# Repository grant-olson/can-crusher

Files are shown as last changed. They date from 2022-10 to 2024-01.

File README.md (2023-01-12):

Welcome to the repository for the most sophisticated robotic aluminum
can crusher that the world has seen!

This is the result of a hobby project that combines CAD design,
Hardware, PCB design, firmware, and software to build an over-the-top
computer-controlled can crusher. I wanted to use a wide variety of skills
on this project instead of going deep into a specific skill.

## In depth 30 minute video on the project

[The Most Technologically Advanced Aluminum Can Crusher In The World](https://youtu.be/nmYN3EZNI_g)

## The Frame

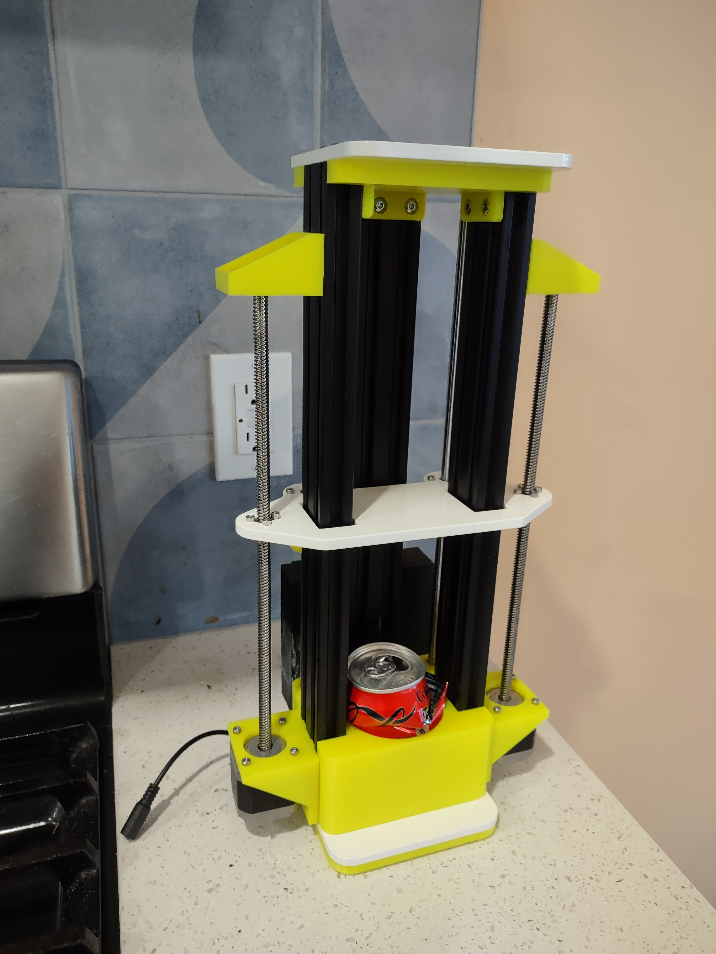
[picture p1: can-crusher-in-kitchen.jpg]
Crusher at home


The frame starts with 3 standard 2040 slotted aluminum extrusions. From there
the major structural elements, the:

* top
* bottom
* crusher plate

Are made from laser cut aluminum.

The rest of the parts are 3D printed.

All design elements are in the included FreeCAD workspace. If you just
want to cut or print the parts refer to the [stl directory](./stl) for
3D print files or the [step directory](./step) for files suitable for laser
cutting.

You will also need two stepper motors with rods and two smooth rods to
assemble the frame in its entirety.

## Stepper Control Board

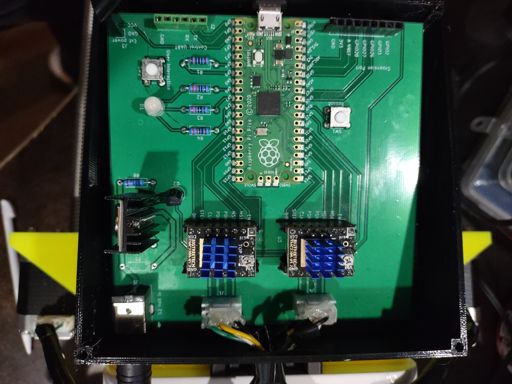
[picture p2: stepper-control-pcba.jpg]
Stepper Controller


To drive the stepper motors I've made a control board powered by a Raspberry
Pi Pico that uses TMC2209 chips to drive the steppers. This allows me to
auto-detect limits of movement.

The design is in KiCad. Gerber files are also included in the repo for
getting PCBs made.

At a high level the control board:

* Initializes the system
* Accepts a small command language over the UART interface.
* Controls the motors appropriately.

I chose the Pi Pico so that I could use the PIO subprocessors to get
extremely reliable control of the stepper signal waves. I'm able to
run those completely deterministicly based on the clock speed where
even IRQs won't affect triggering.

To build the software:

* Set up your computer to build for Pico projects.
* `cd firmware/pico`
* `mkdir build`
* `cd build`
* `cmake ..`
* `make`
* `picotool load can-crusher.uf2 && picotool reboot`

If you have stepper motors hooked up they should perform a minor
up/down jogging of the motors upon reboot. Use this to see if the
code is actually running without the admin consoles set up.

## High level control and UI

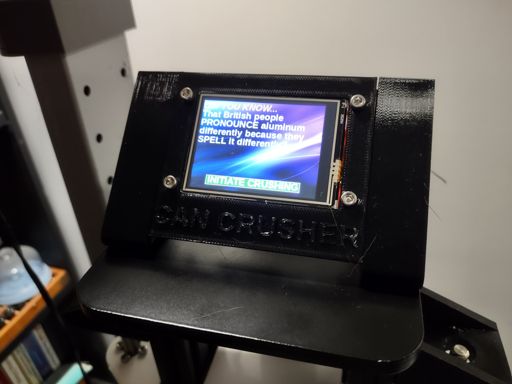
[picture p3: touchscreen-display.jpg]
Head Unit


For the high level control and UI I've written a program for a Raspberry
Pi that shows a minimal display on a TFT-LCD with touchscreen to allow users
to interact.

To make a compact display I've created a Hat for a Pi Zero board that allows
you to mount the parts together directly that is also released as a KiCad file.

Due to continuing Raspberry Pi shortages I'd like to build some
alternate versions of the control boards for other SBCs. The software
itself iswritten in python and should be portable to pretty much any
linux system. There are only 3 hardware requirements so I expect other
boards will be easy to integrate:

* Ability to have a hardware level SPI control with /dev/spidevX.X exposed.

* A kernel that supports ADS7846  touch screens and provides integration with
    `evdev` to read touch screen events.

* A hardware serial/uart port capable of running at 115200 baud.

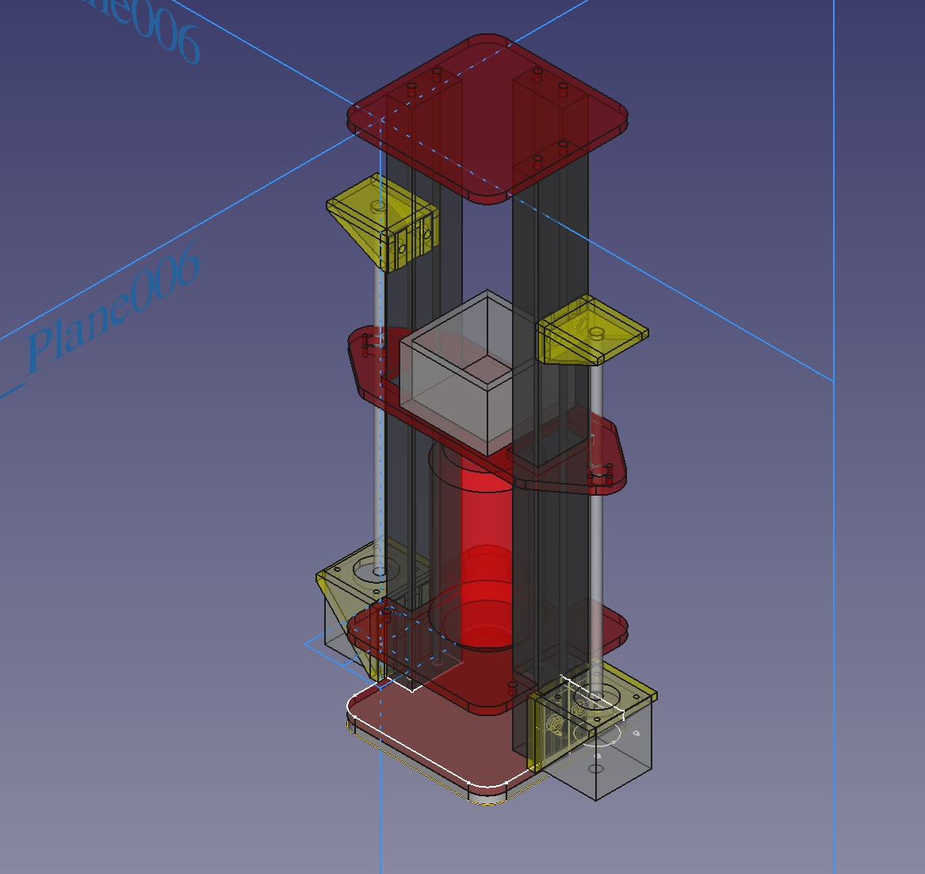
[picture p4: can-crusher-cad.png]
Cad render


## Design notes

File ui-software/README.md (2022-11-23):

#UI Software

The current UI software runs on a Raspberry Pi Zero with an attached
TFT LCD Touchscreen. There are a variety of vendors that sell the same
style 320x240 with the same pinout on Amazon, eBay, and
AliExpress. Although it can be wired up manually there is also a Pi
Hat in the kicad section of the project to make an adapter PCBA.

It communicates with the main control software via a serial connection
and receives its power from the base unit.

There are three programs that are important:

`slide-maker` pre-builds optimized versions of graphics to make it
easier to run efficiently on the moderately slow Raspberry Pi Zero.

`can-crusher-pi` runs the code for the specified head unit
configuration above.

`can-crusher-cli` provides a simple way to run the code directly from
your dev computer with a USB-to-UART dongle, which is much easier than
trying to remotely program on the Pi Zero.

The `can_crusher` directory contains the python modules that do all
the heavy work.

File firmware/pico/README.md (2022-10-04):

# Pico firmware for can crusher project.

Assuming you've set up a Pico development environment as described in
[Getting Started with
Pico](https://datasheets.raspberrypi.com/pico/getting-started-with-pico.pdf):

Then build the project standard CMake style:

```
mkdir build
cd build
cmake ..
make
```

And you will have a UF2 file ready for installation.

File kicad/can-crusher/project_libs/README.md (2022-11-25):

The following libraries are from SnapEDA and can't be included on github.

# R1966 power switch

1. Download from https://www.snapeda.com/parts/R1966ABLKBLKGR/E-Switch/view-part/

2. Extract to the subdirectory `R1966` here.

# 3522 Fuse Holder

1. Download from https://www.snapeda.com/parts/3522-2/Keystone%20Electronics/view-part/

2. Extract to the subdirectory `3522` here.

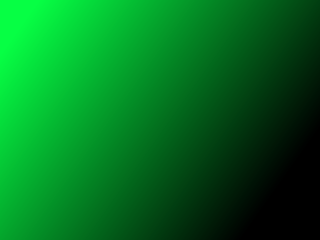
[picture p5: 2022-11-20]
ui-software/input/backgrounds/green_background.png

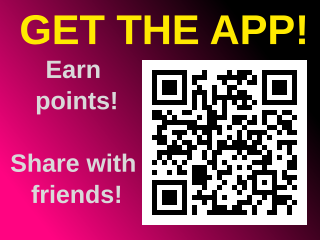
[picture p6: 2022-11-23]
ui-software/input/png/get_the_app.png

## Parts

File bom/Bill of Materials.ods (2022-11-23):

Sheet: Hardware
Part | Quantity | Function
Button Head M5 * 8mm | 22 | Attach 3D Parts to Extrusions
M5 T-Slot Nut | 22
2040 Aluminum Extrusion | 3
M5 ??? | 6 | Attach frame bottom to Extrusions
M5 ??? | 6 | Attach frame top to Extrusions
M3 ??? | 8 | Attach steppers to stepper holders
M3 ??? | 6 | Attach bearing holders to crusher plate
10mm straight rod x 350mm | 2 | Guide Rods
Nema 17 Stepper motors with 30mm threaded Rods | 2
Raspbery Pi Zero | 1 | UX computer
Bearings | 2
12 Volt power supply | 1
M3 x 14 | 4 | Connect PCB Case Front to Back

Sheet: 3D Prints
Part | Quantity
Rod Holder | 2
Frame Bottom | 1
Frame Top | 1
Frame Base | 1
Servo Holder | 2
Crusher | 1

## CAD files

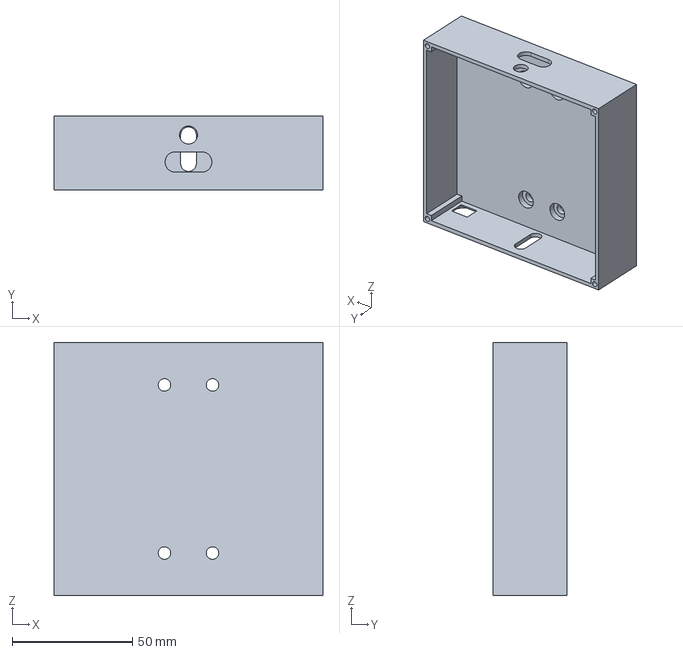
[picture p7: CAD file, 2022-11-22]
freecad/can-crusher.FCStd
112.0 x 31.0 x 105.5 mm

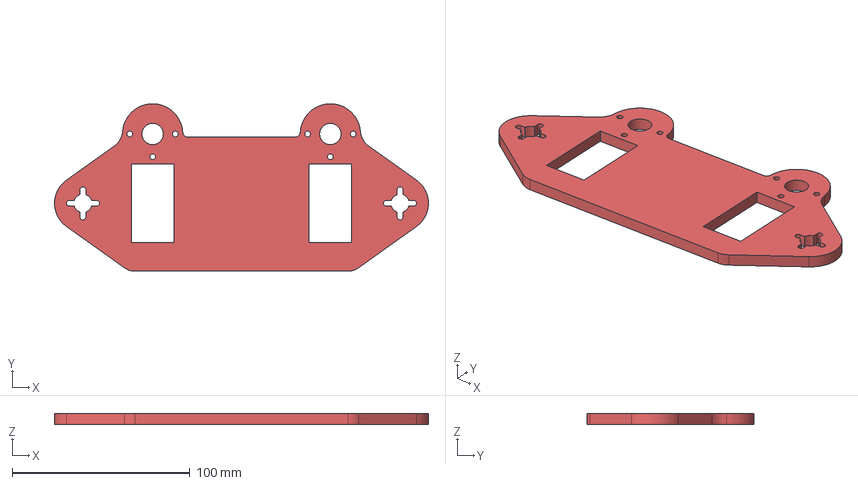
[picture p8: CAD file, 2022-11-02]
step/crusher-element-with-bearing-holders.step
210.4 x 94.2 x 6.00 mm

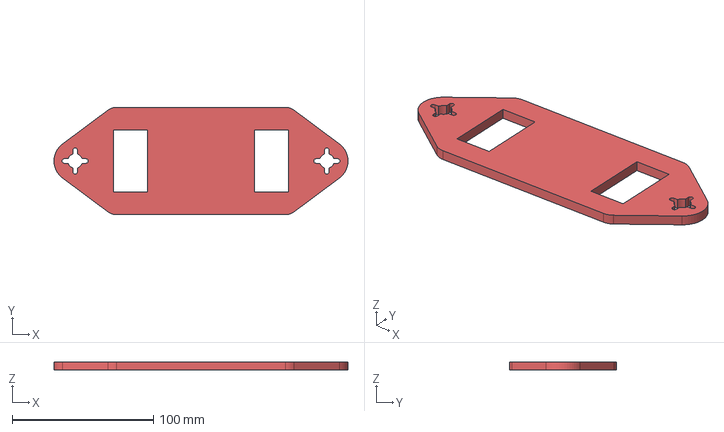
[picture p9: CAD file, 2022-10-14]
step/crusher-element-laser.step
208.3 x 76.0 x 6.00 mm

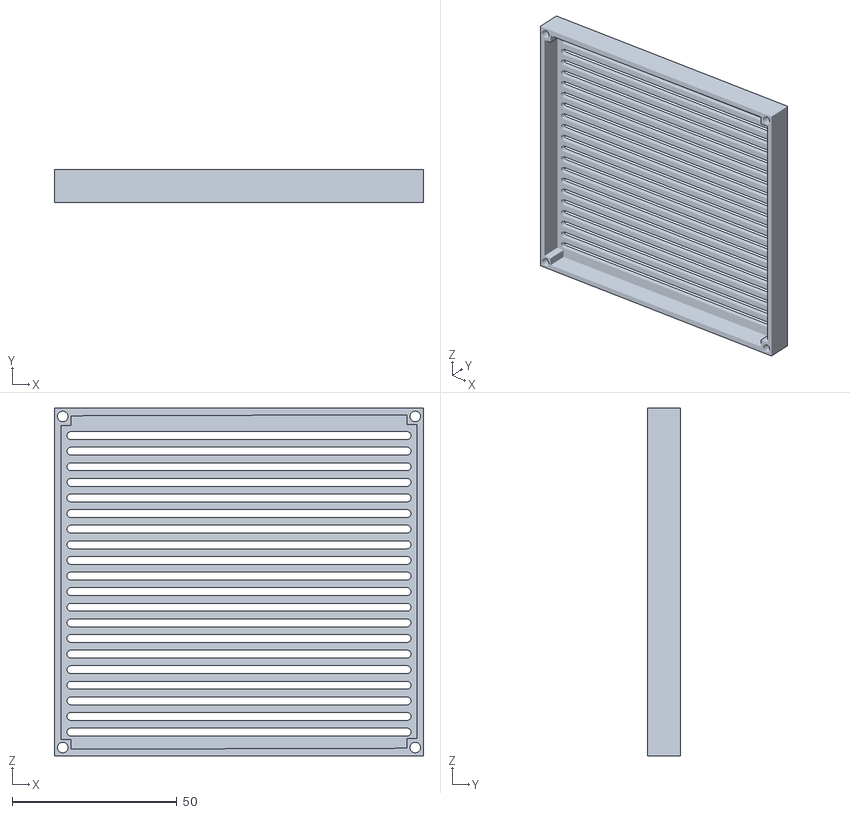
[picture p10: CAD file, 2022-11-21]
stl/pcb-holder-lid.stl
112.0 x 10.0 x 105.5

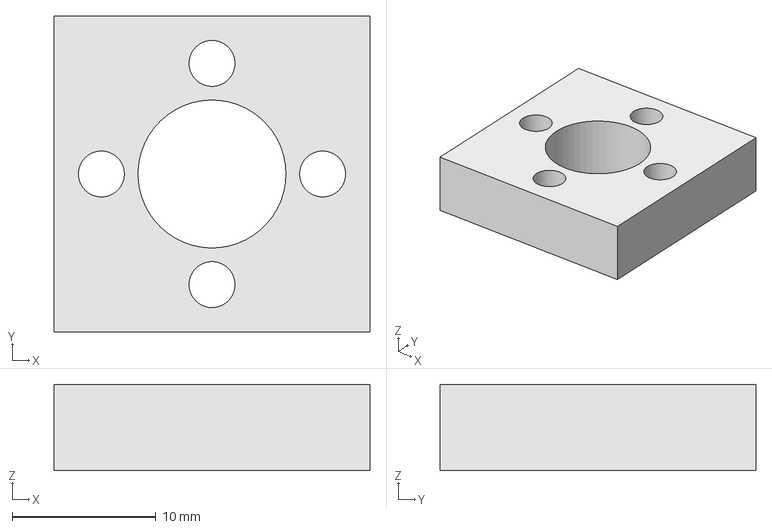
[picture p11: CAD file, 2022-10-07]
step/lead_holder_test.step
22.0 x 22.0 x 6.00 mm

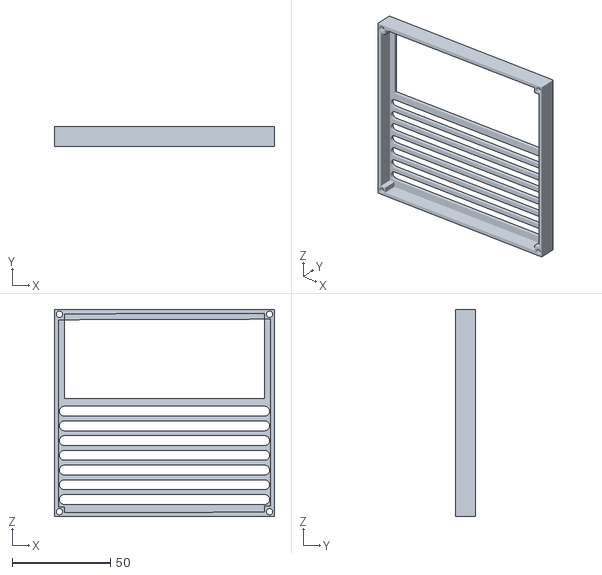
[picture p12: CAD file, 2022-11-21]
stl/ALT-pcb-holder-lid-with-dev-button-access.stl
112.0 x 10.0 x 105.5

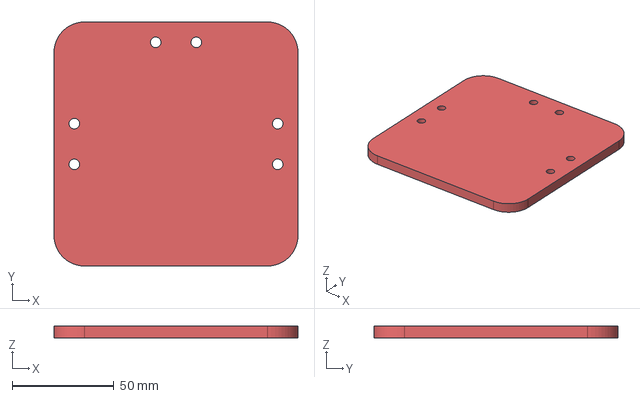
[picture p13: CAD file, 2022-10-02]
step/frame-ends.step
120.0 x 120.0 x 6.00 mm

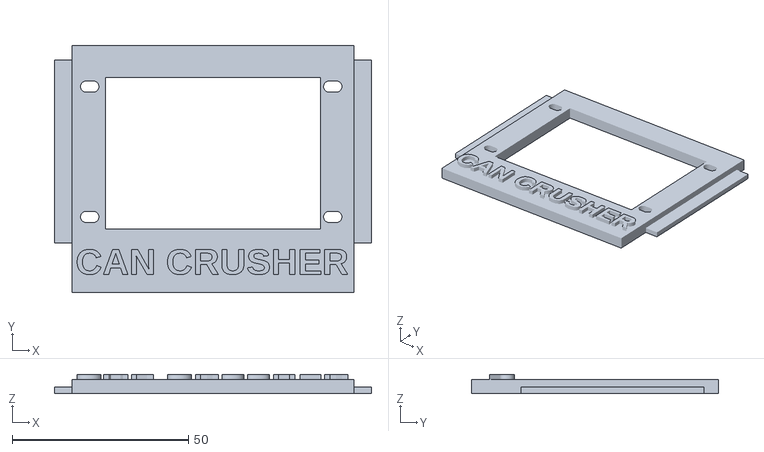
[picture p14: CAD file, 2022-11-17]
stl/touch-screen-front.stl
90.0 x 70.0 x 5.40

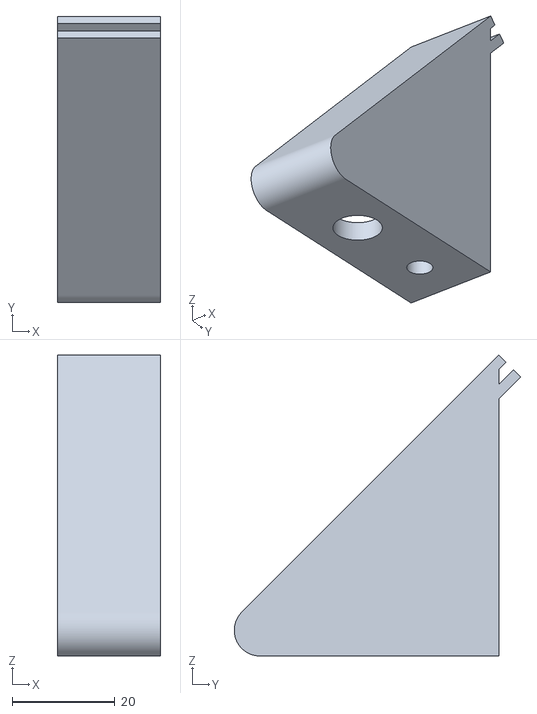
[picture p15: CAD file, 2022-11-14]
stl/touch-screen-right.stl
20.0 x 55.7 x 58.5

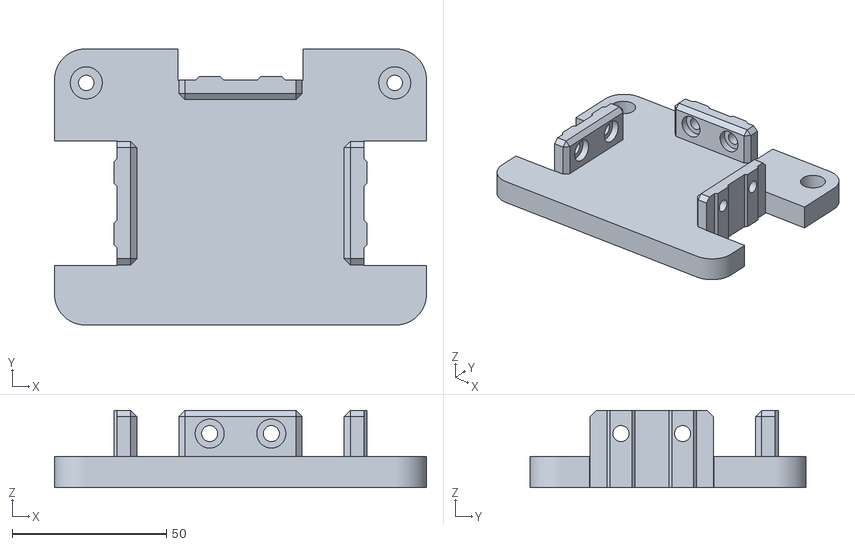
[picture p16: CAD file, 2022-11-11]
stl/smooth-rod-holder-top.stl
120.6 x 89.5 x 25.0

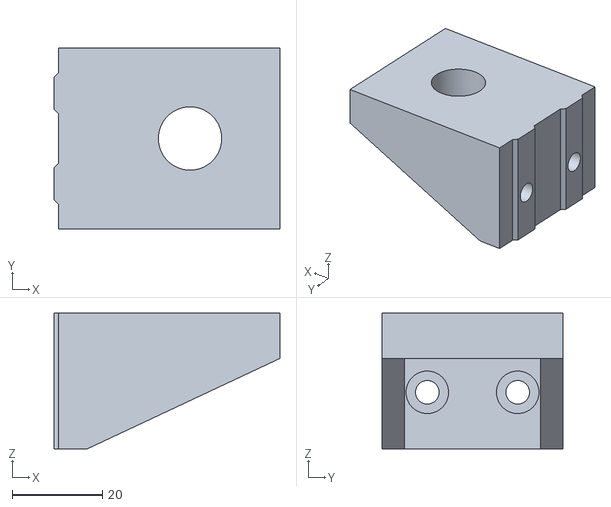
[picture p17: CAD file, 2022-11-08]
stl/rod-holder.stl
50.0 x 40.0 x 30.0

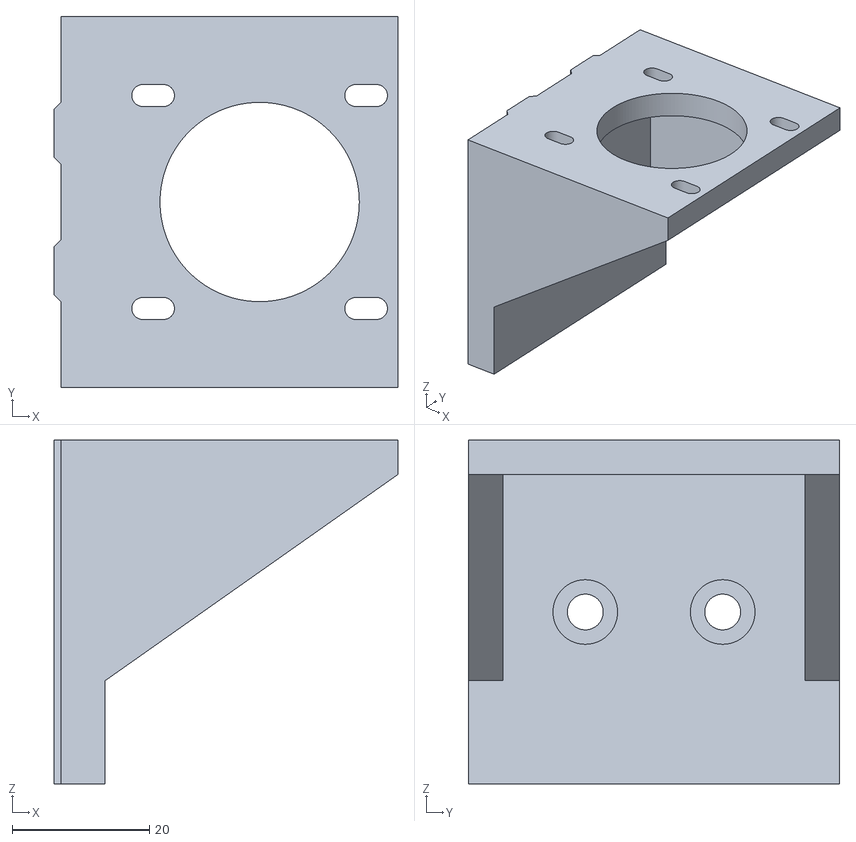
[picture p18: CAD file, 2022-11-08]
stl/stepper-holder.stl
50.0 x 54.0 x 50.0

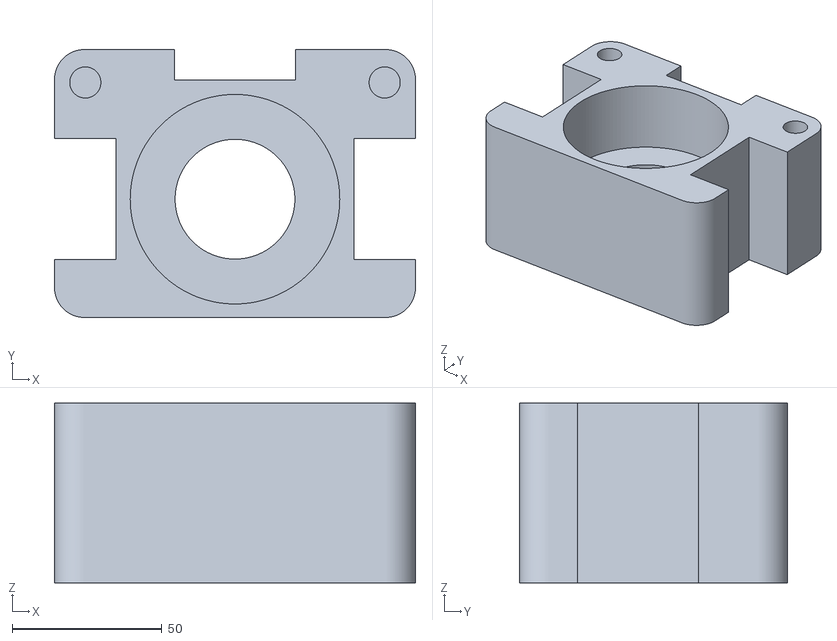
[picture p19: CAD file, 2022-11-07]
stl/can-holder.stl
120.6 x 89.5 x 60.0

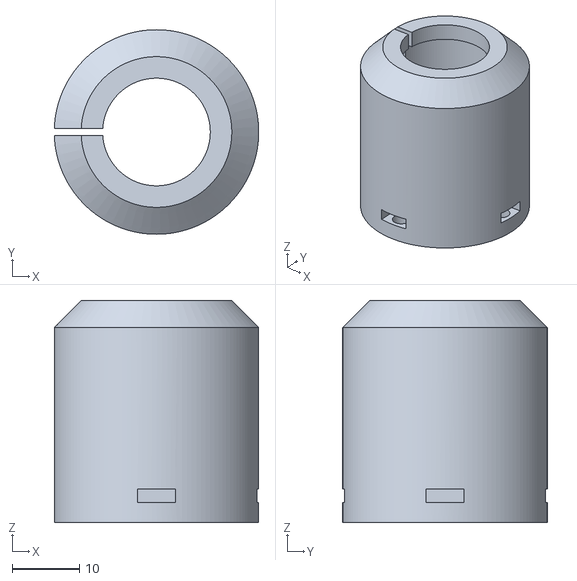
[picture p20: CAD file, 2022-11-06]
stl/vertical-bearing-holder.stl
30.4 x 30.4 x 33.0

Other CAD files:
stl/ALT-pcb-holder-pico-on-header-socket.stl
stl/pcb-holder.stl
step/crusher-element-cnc.step
stl/touch-screen-left.stl
stl/base-with-feet.stl
stl/crusher-element-with-bearing-holders.stl
stl/crusher-plate.stl
stl/frame-plates.stl
stl/test-rail-guide.stl
stl/weight-tray.stl

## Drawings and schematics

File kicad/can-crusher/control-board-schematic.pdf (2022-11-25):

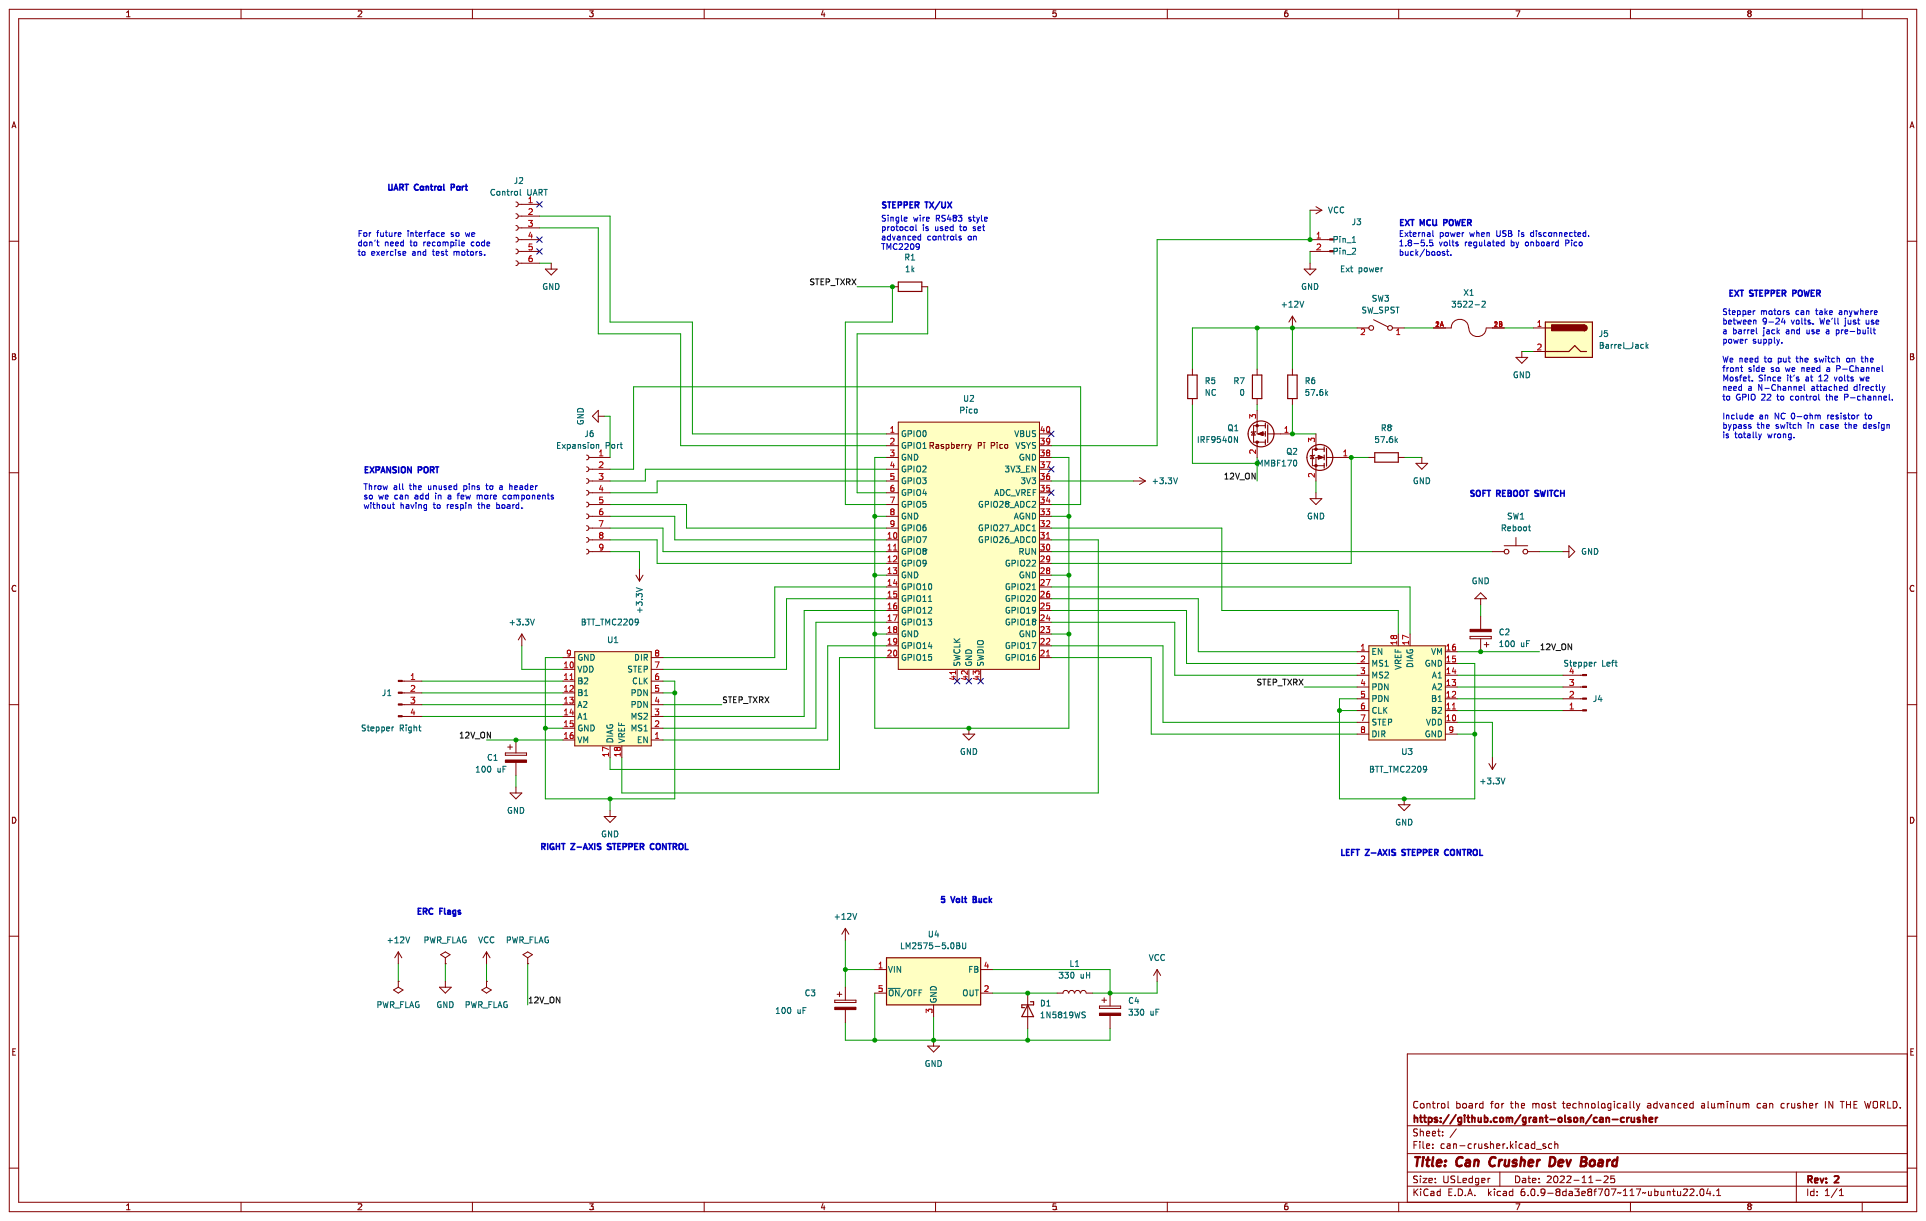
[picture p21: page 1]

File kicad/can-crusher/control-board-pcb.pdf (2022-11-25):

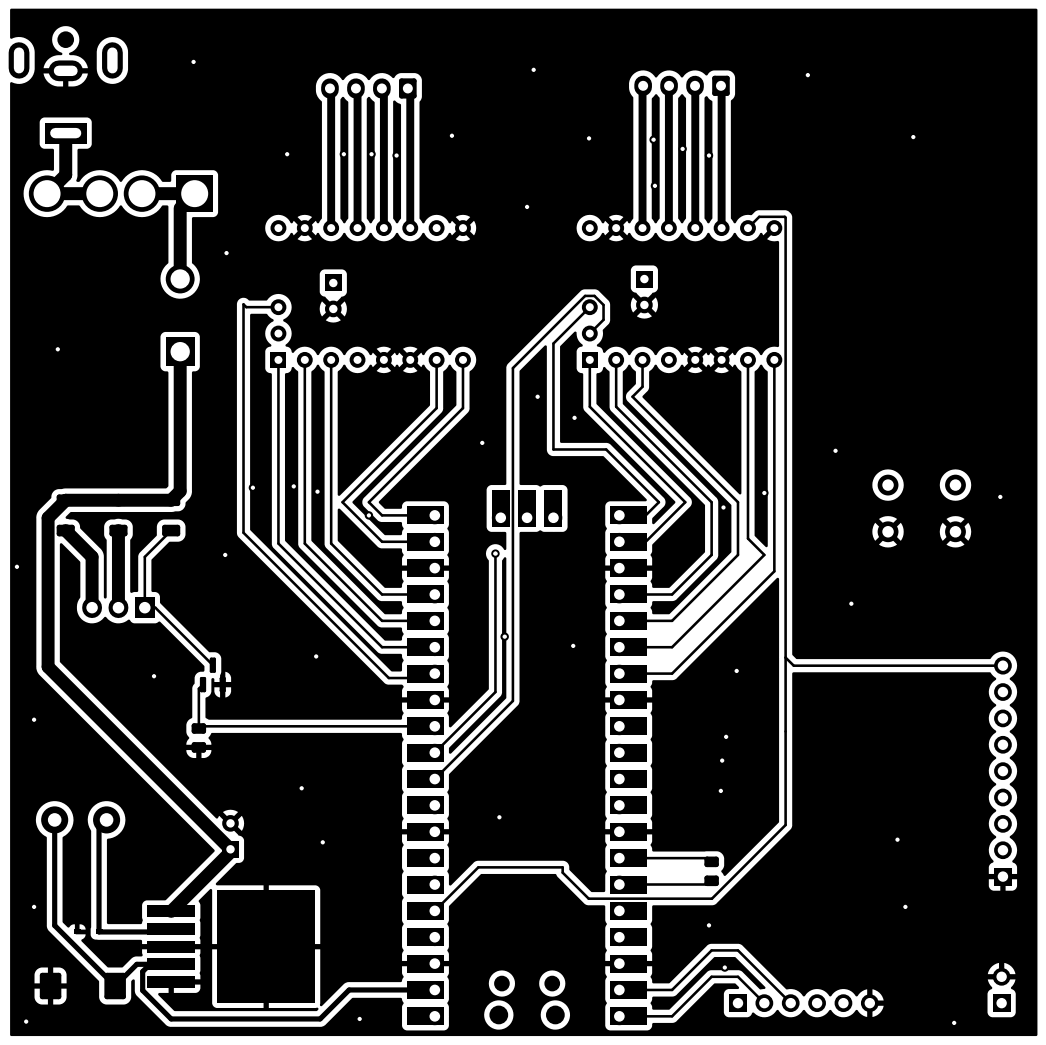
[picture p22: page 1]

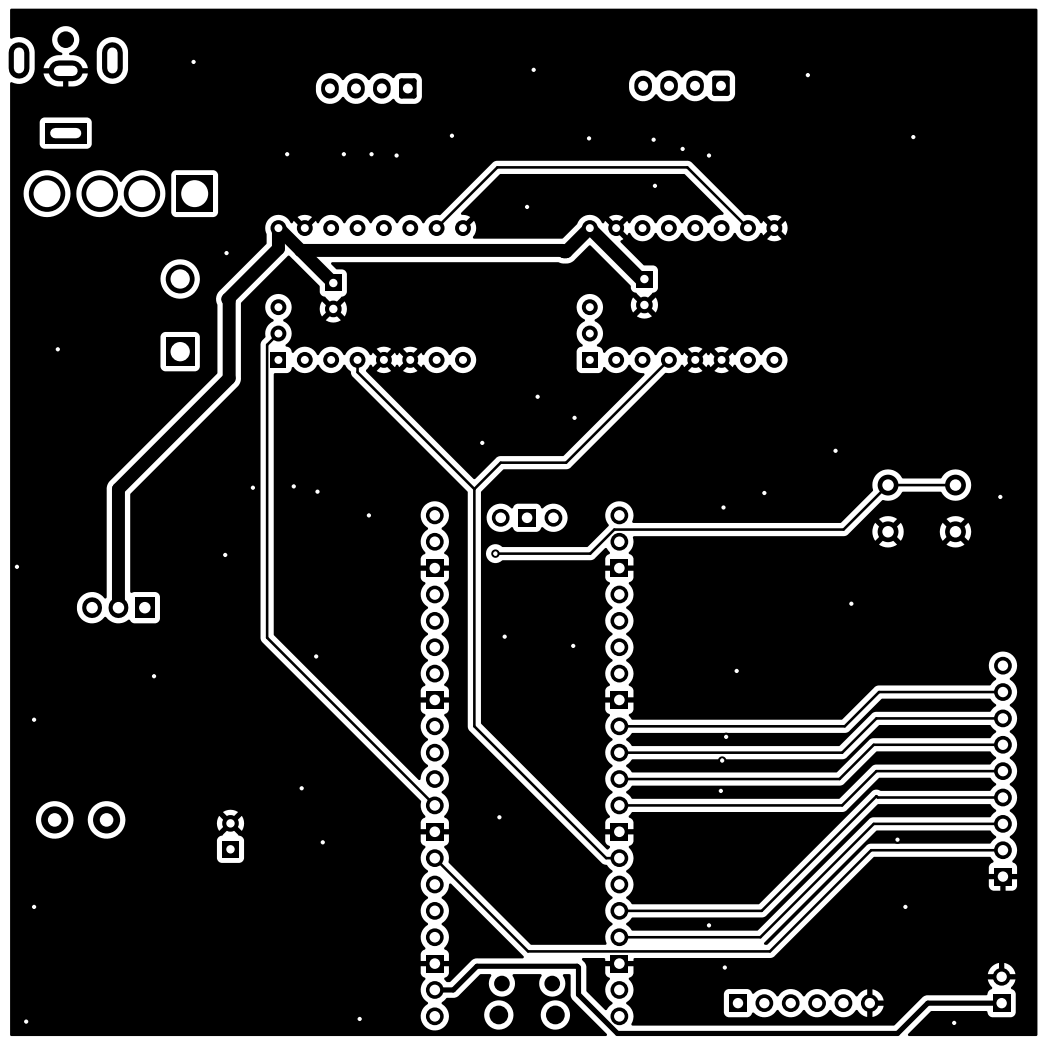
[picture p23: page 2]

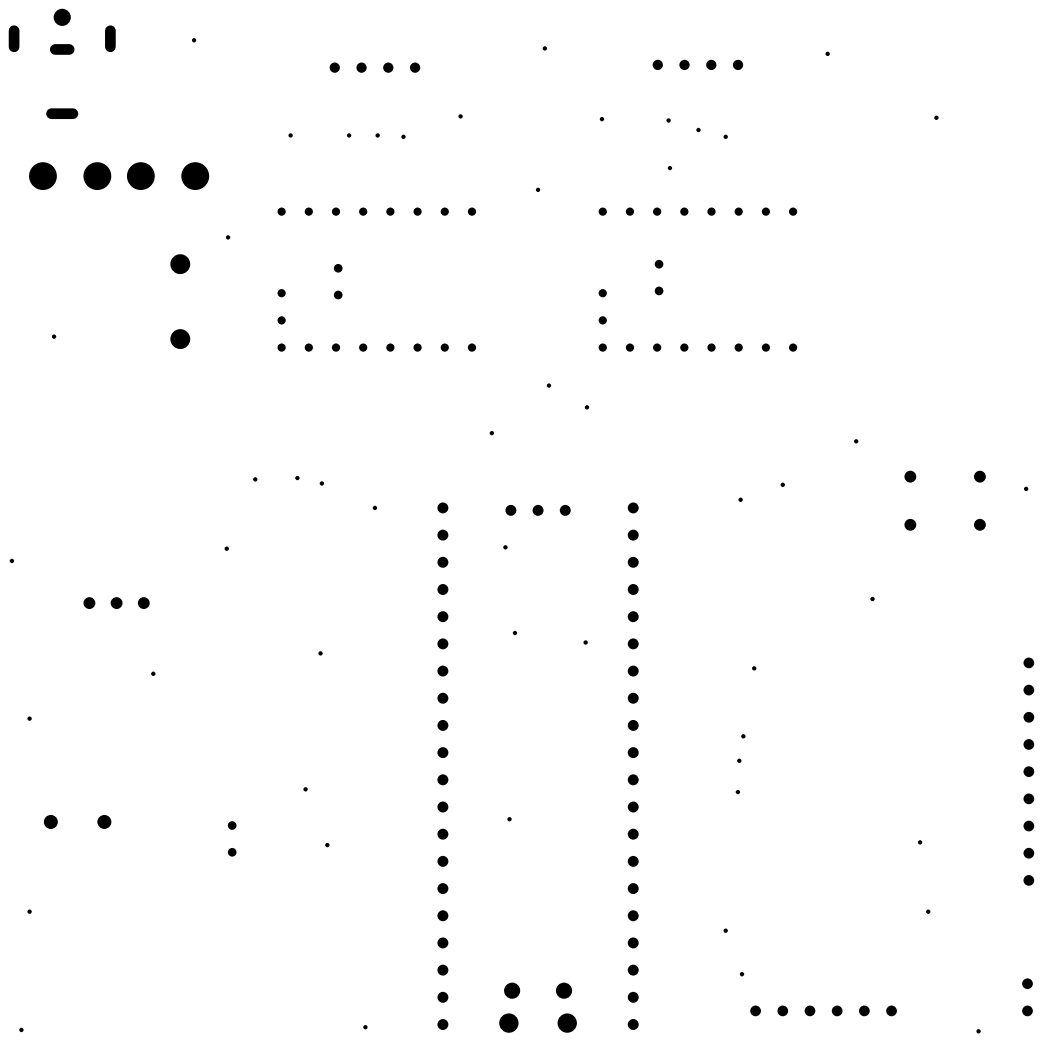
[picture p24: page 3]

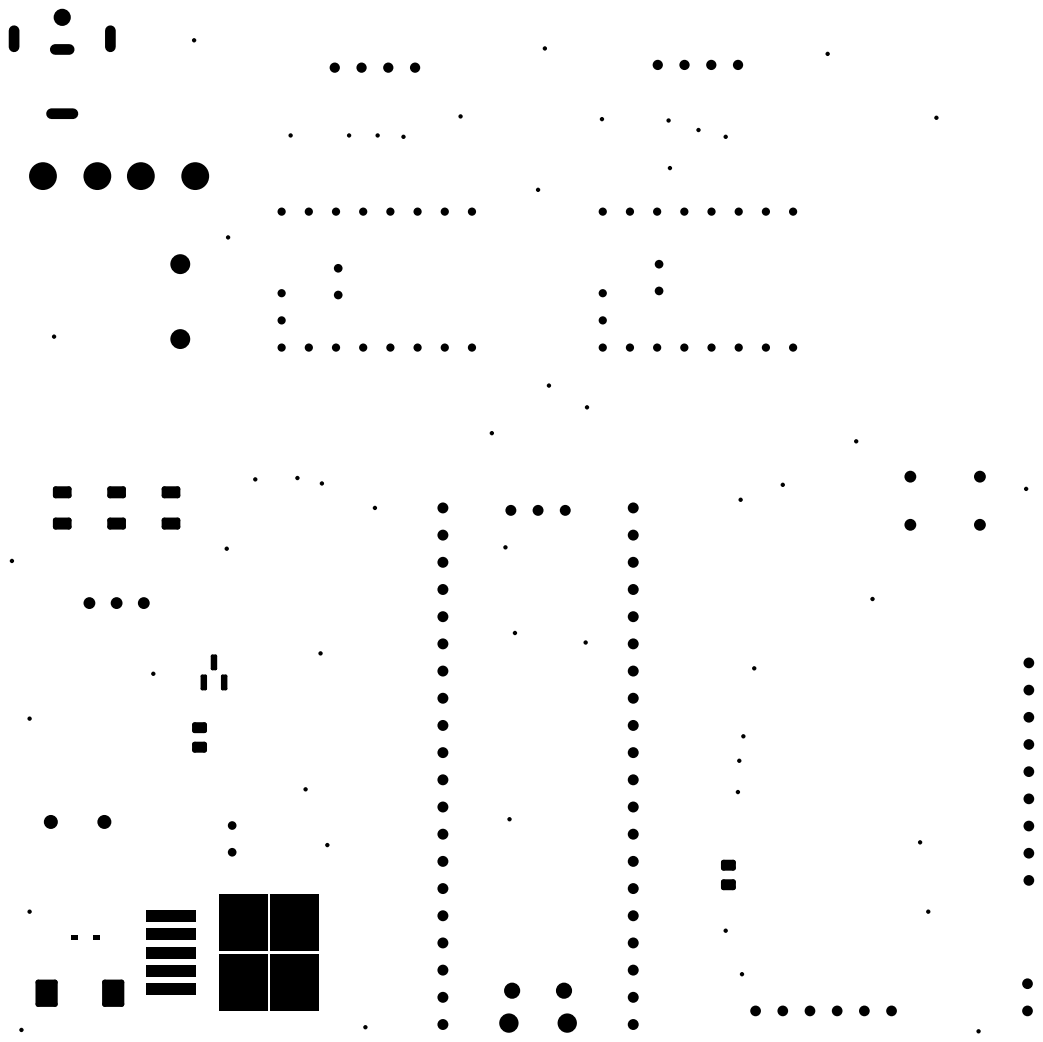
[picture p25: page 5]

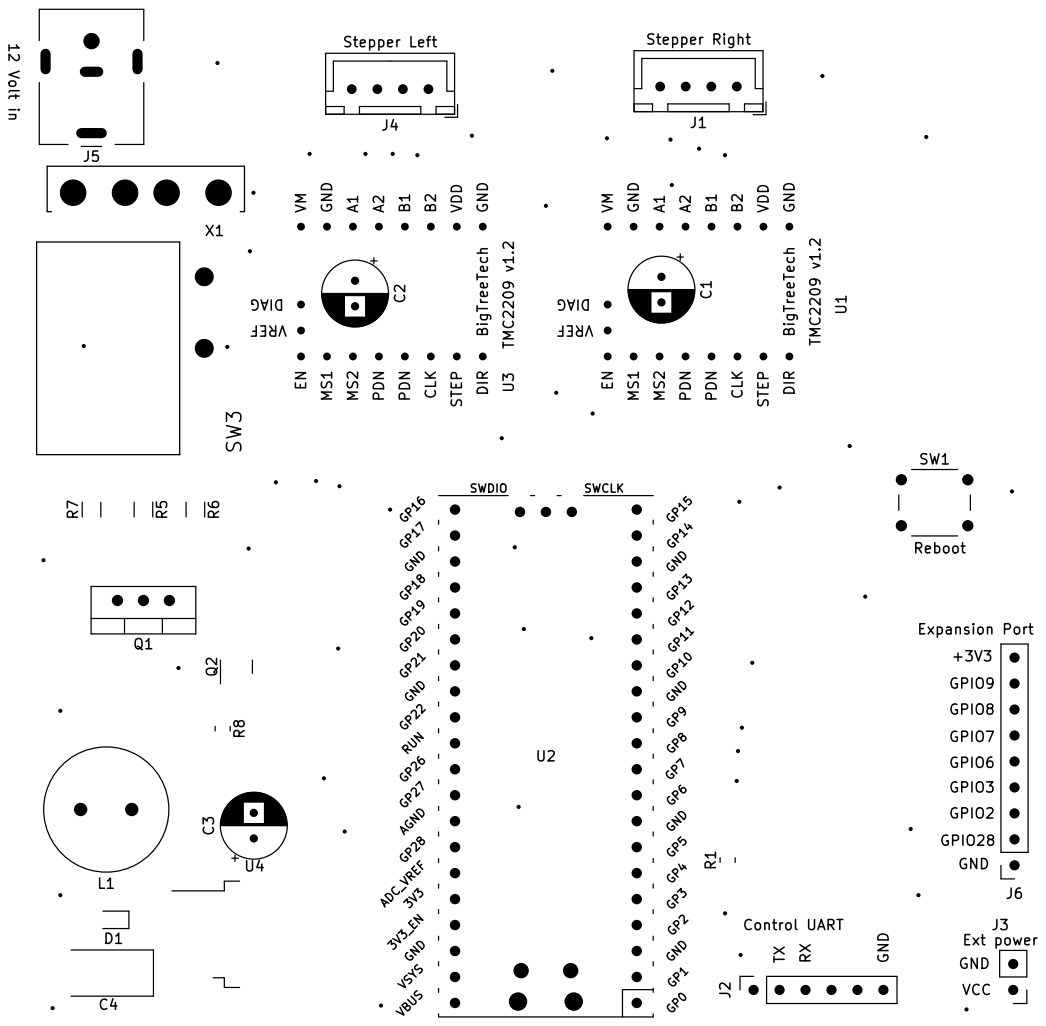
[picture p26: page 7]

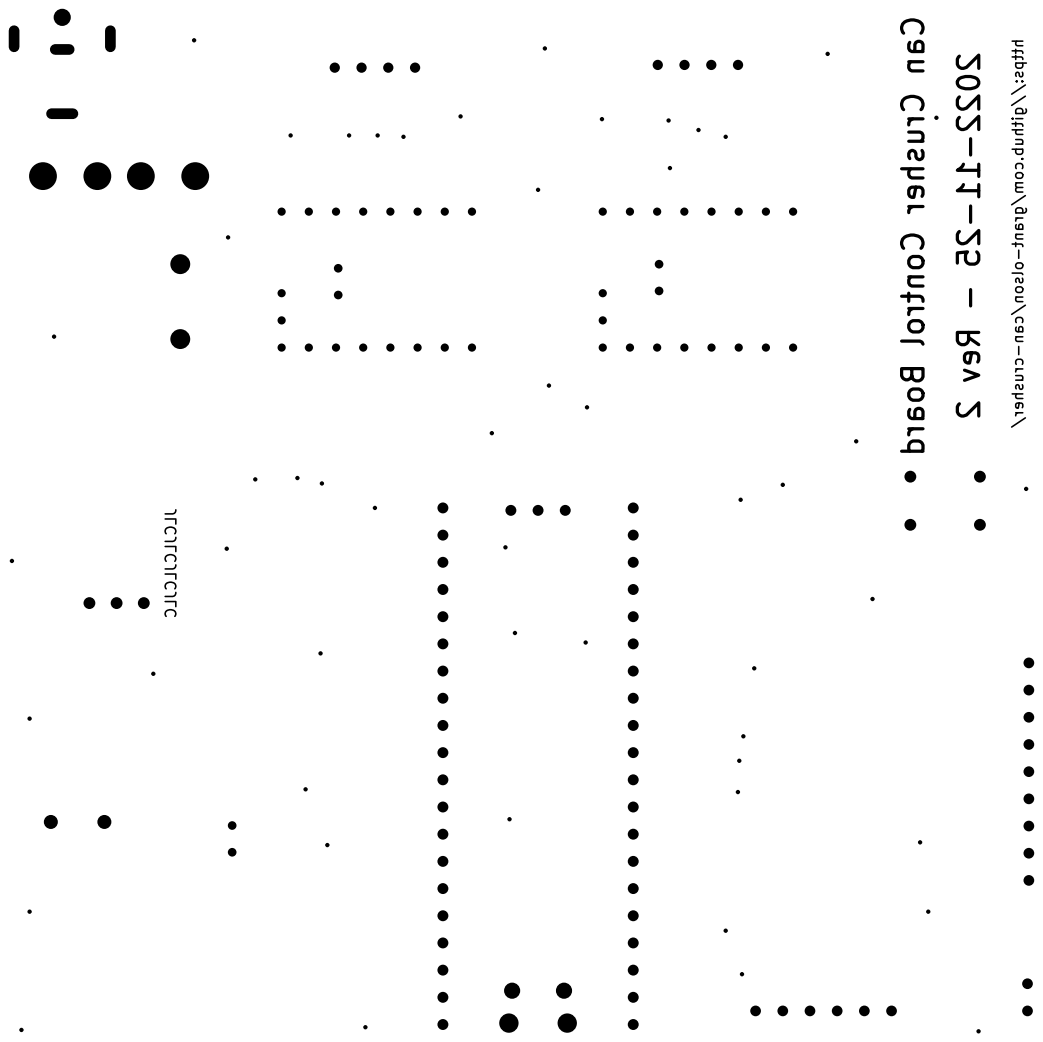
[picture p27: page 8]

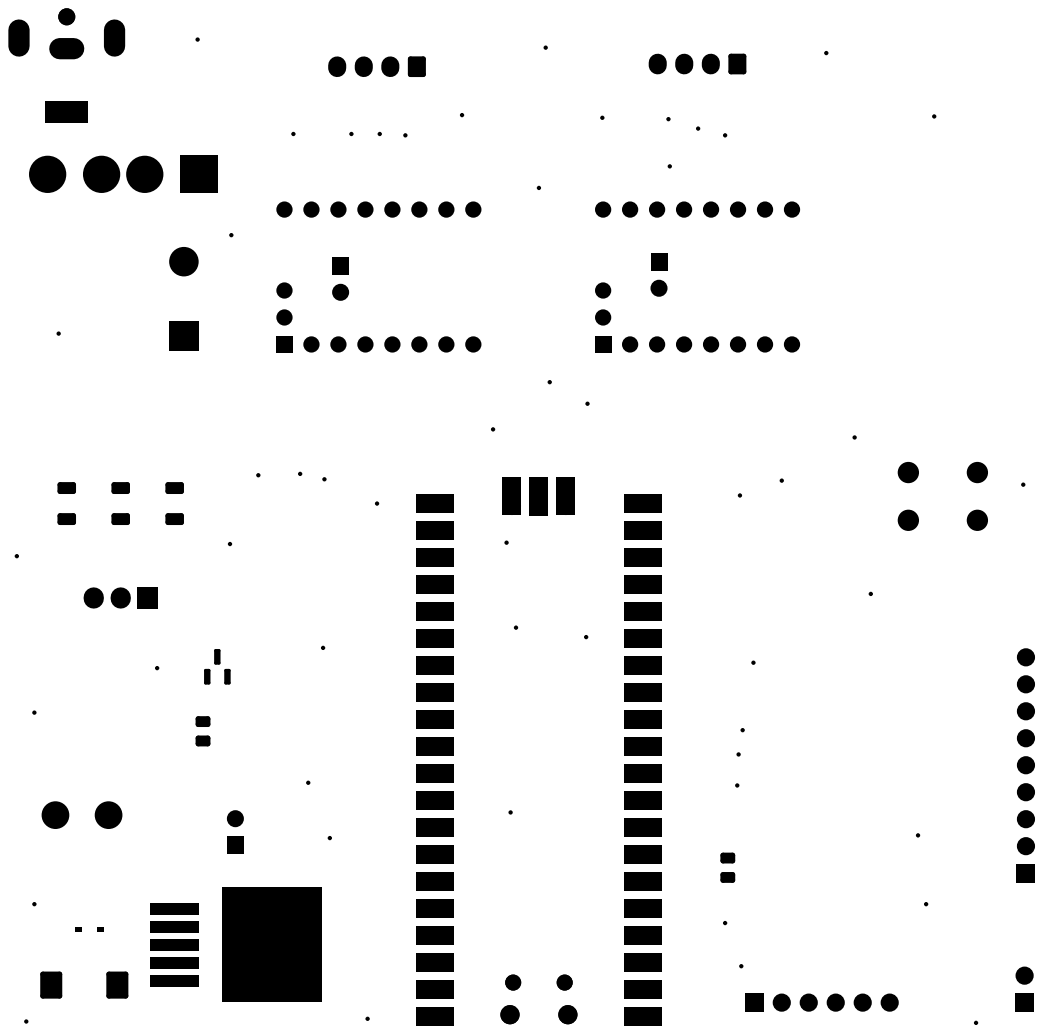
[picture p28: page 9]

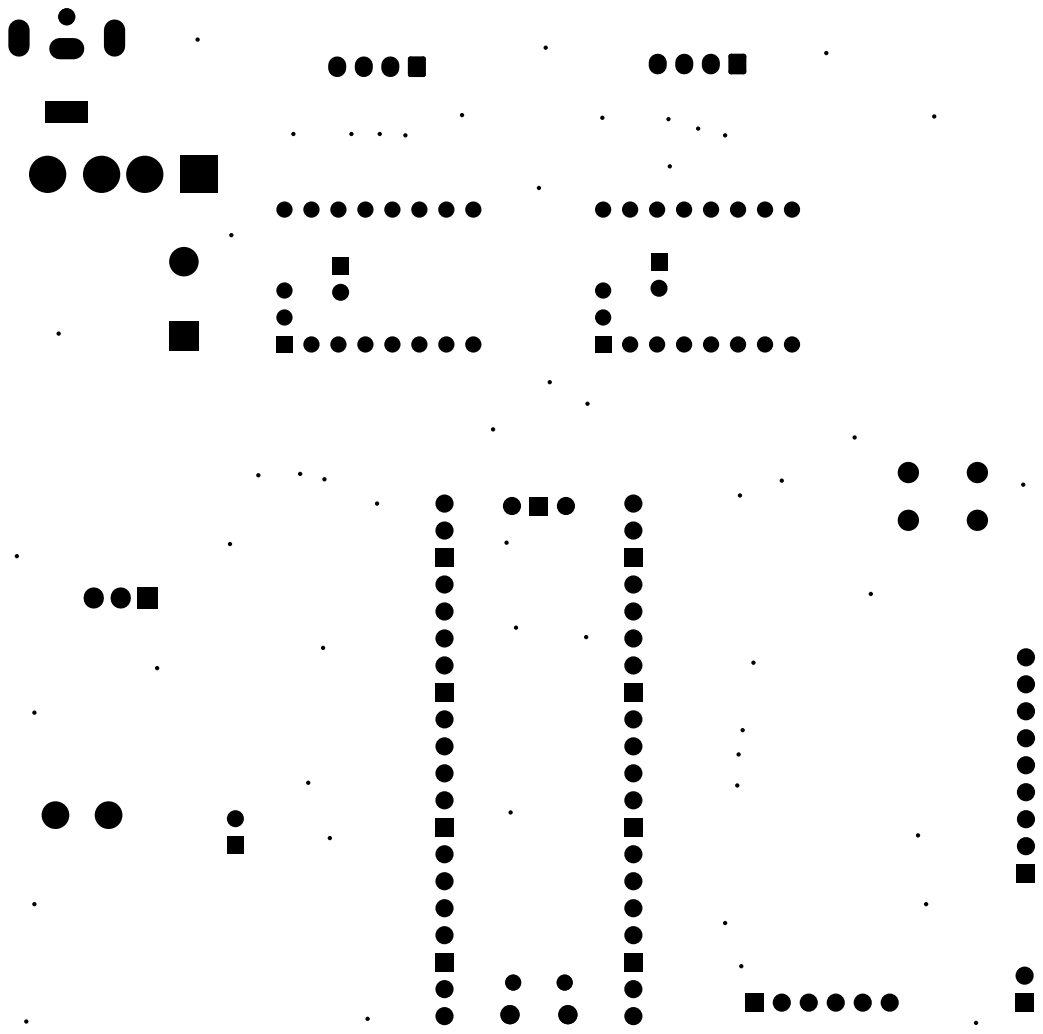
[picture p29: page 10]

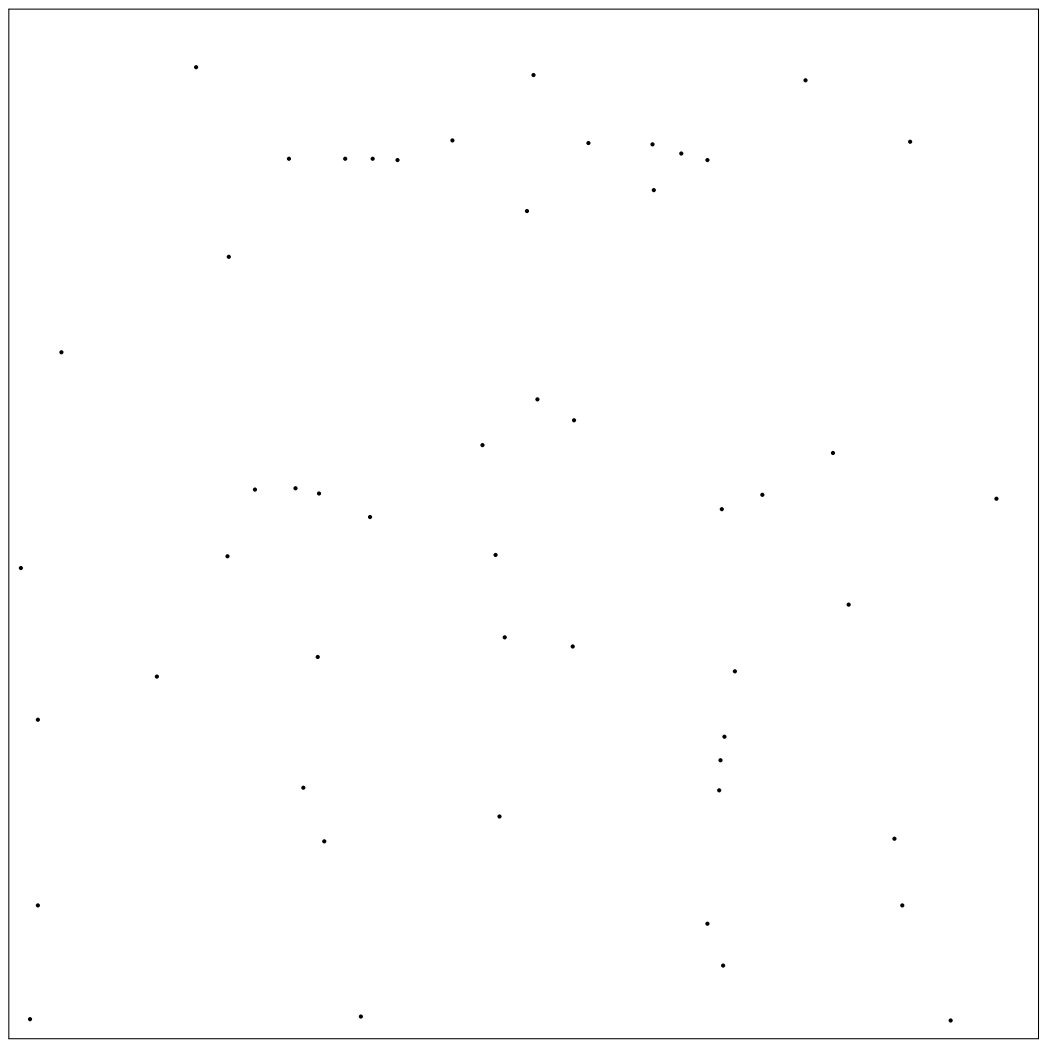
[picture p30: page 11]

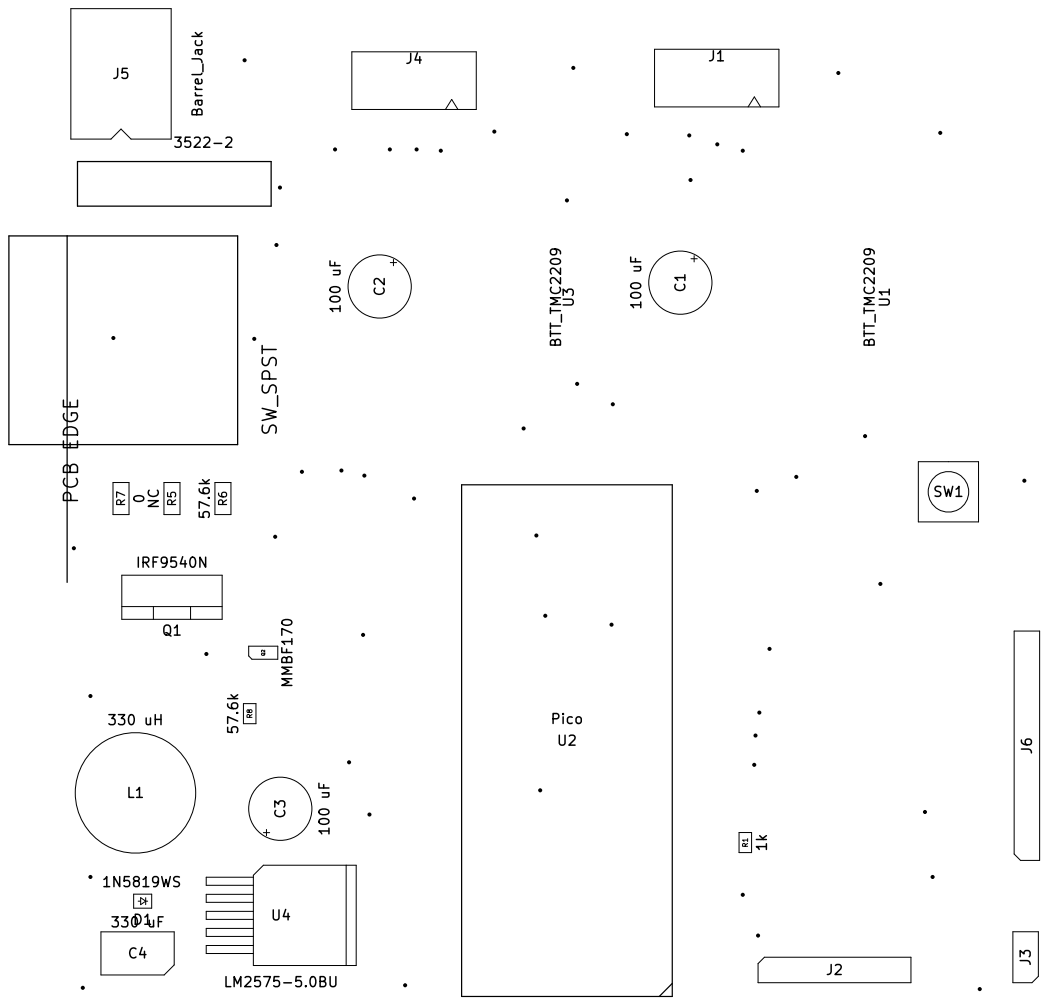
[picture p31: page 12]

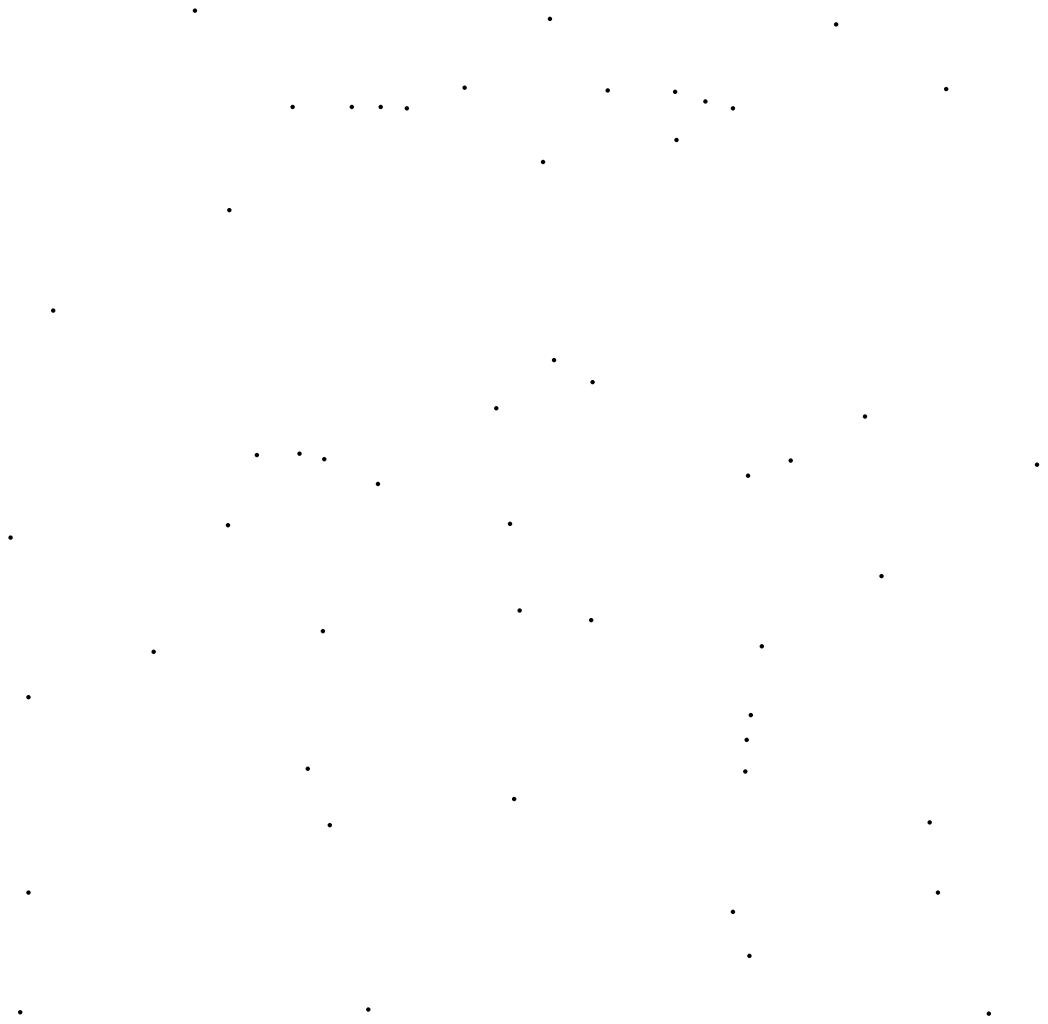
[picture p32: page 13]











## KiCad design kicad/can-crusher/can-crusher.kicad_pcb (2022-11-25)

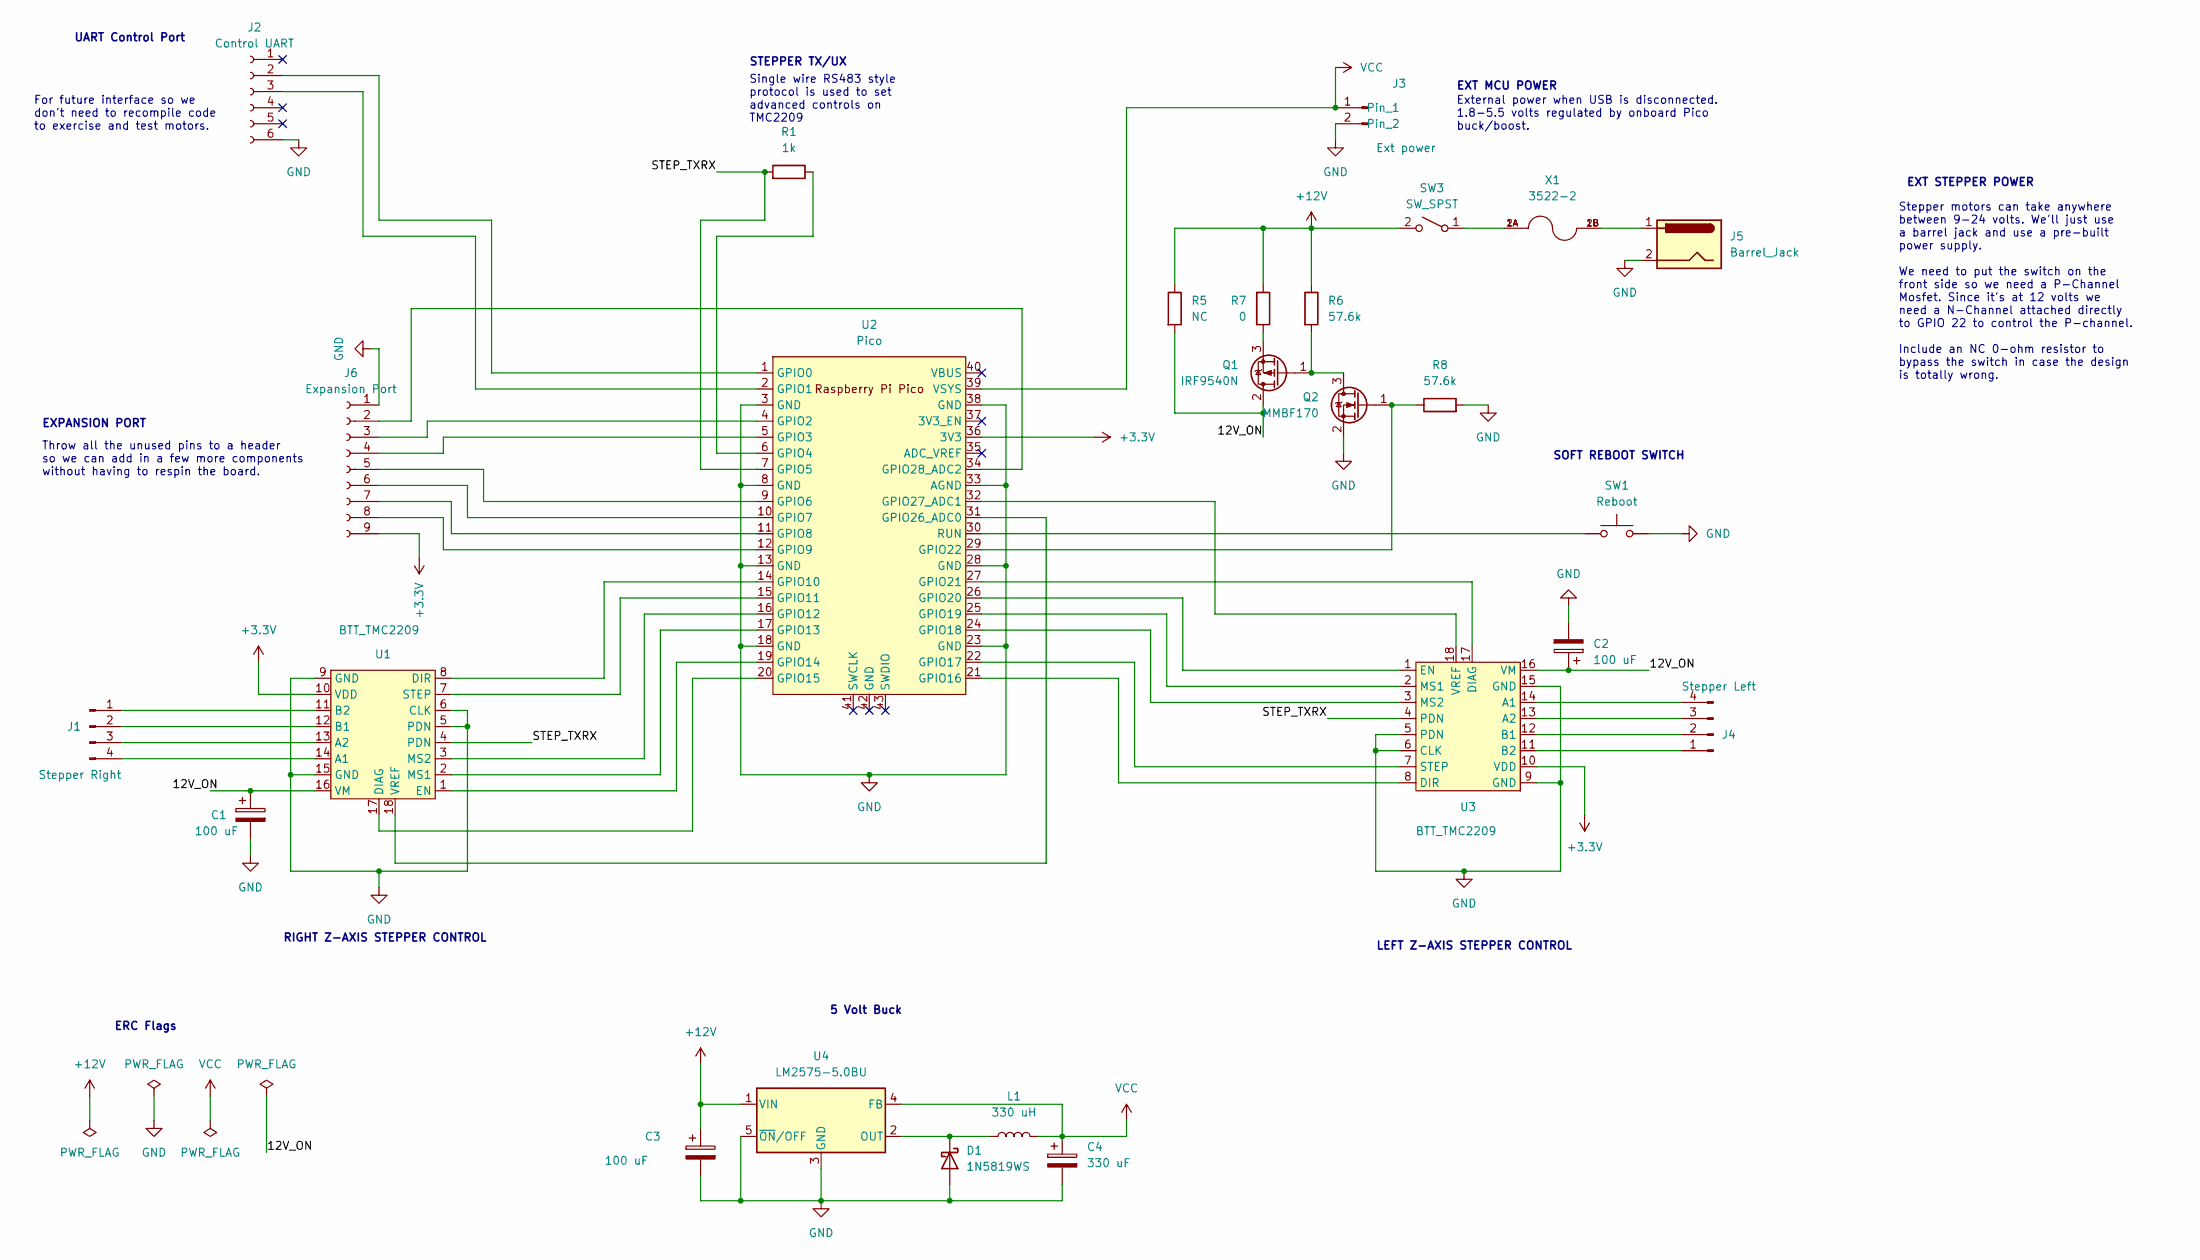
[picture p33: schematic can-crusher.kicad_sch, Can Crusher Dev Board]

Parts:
C1, C2, C3: 100 uF; CP_Radial_D6.3mm_P2.50mm
C4: 330 uF; CP_EIA-7343-43_Kemet-X
D1: 1N5819WS; D_SOD-323
J1: Stepper Right; JST_XH_B4B-XH-A_1x04_P2.50mm_Vertical
J2: Control UART; PinSocket_1x06_P2.54mm_Vertical
J3: Ext power; PinHeader_1x02_P2.54mm_Vertical
J4: Stepper Left; JST_XH_B4B-XH-A_1x04_P2.50mm_Vertical
J5: Barrel_Jack; BarrelJack_CUI_PJ-063AH_Horizontal
J6: Expansion Port; PinSocket_1x09_P2.54mm_Vertical
L1: 330 uH; L_Radial_D12.0mm_P5.00mm_Fastron_11P
Q1: IRF9540N; TO-220-3_Vertical
Q2: MMBF170; SOT-23
R1: 1k; R_0805_2012Metric
R5: NC; R_1206_3216Metric
R6: 57.6k; R_1206_3216Metric
R7: 0; R_1206_3216Metric
R8: 57.6k; R_0805_2012Metric
SW1: Reboot; SW_PUSH_6mm_H4.3mm
SW3: SW_SPST; SW_R1966ABLKBLKGR
U1, U3: BTT_TMC2209
U2: Pico; RPi_Pico_SMD_TH
U4: LM2575-5.0BU; TO-263-5_TabPin3
X1: 3522-2; FUSE_3522-2; PARTREV J

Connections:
+3.3V: J6.9, U1.10 (VDD), U2.36 (3V3), U3.10 (VDD)
+12V: C3.1, R5.1, R6.1, R7.2, SW3.2 (B), U4.1 (VIN)
/12V_ON: C1.1, C2.1, Q1.2 (D), R5.2, U1.16 (VM), U3.16 (VM)
/STEP_TXRX: R1.2, U1.4 (PDN), U2.7 (GPIO5), U3.4 (PDN)
GND: C1.2, C2.2, C3.2, C4.2, D1.2 (A), J2.6, J3.2, J5.2, J6.1, Q2.2 (S), R8.2, SW1.2, U1.5 (PDN), U1.6 (CLK), U1.9 (GND), U1.15 (GND), U2.3 (GND), U2.8 (GND), U2.13 (GND), U2.18 (GND), U2.23 (GND), U2.28 (GND), U2.33 (AGND), U2.38 (GND), U3.5 (PDN), U3.6 (CLK), U3.9 (GND), U3.15 (GND), U4.3 (GND), U4.5 (~ON/OFF)
unnamed: D1.1 (K), L1.1, U4.2 (OUT)
unnamed: J1.1, U1.11 (B2)
unnamed: J1.2, U1.12 (B1)
unnamed: J1.3, U1.13 (A2)
unnamed: J1.4, U1.14 (A1)
unnamed: J2.2, U2.1 (GPIO0)
unnamed: J2.3, U2.2 (GPIO1)
unnamed: J4.1, U3.11 (B2)
unnamed: J4.2, U3.12 (B1)
unnamed: J4.3, U3.13 (A2)
unnamed: J4.4, U3.14 (A1)
unnamed: J5.1, X1.1B, X1.2B
unnamed: J6.2, U2.34 (GPIO28_ADC2)
unnamed: J6.3, U2.4 (GPIO2)
unnamed: J6.4, U2.5 (GPIO3)
unnamed: J6.5, U2.9 (GPIO6)
unnamed: J6.6, U2.10 (GPIO7)
unnamed: J6.7, U2.11 (GPIO8)
unnamed: J6.8, U2.12 (GPIO9)
unnamed: Q1.1 (G), Q2.3 (D), R6.2
unnamed: Q1.3 (S), R7.1
unnamed: Q2.1 (G), R8.1, U2.29 (GPIO22)
unnamed: R1.1, U2.6 (GPIO4)
unnamed: SW1.1, U2.30 (RUN)
unnamed: SW3.1 (A), X1.1A, X1.2A
unnamed: U1.1 (EN), U2.19 (GPIO14)
unnamed: U1.2 (MS1), U2.17 (GPIO13)
unnamed: U1.3 (MS2), U2.16 (GPIO12)
unnamed: U1.7 (STEP), U2.15 (GPIO11)
unnamed: U1.8 (DIR), U2.14 (GPIO10)
unnamed: U1.17 (DIAG), U2.20 (GPIO15)
unnamed: U1.18 (VREF), U2.31 (GPIO26_ADC0)
unnamed: U2.21 (GPIO16), U3.8 (DIR)
unnamed: U2.22 (GPIO17), U3.7 (STEP)
unnamed: U2.24 (GPIO18), U3.3 (MS2)
unnamed: U2.25 (GPIO19), U3.2 (MS1)
unnamed: U2.26 (GPIO20), U3.1 (EN)
unnamed: U2.27 (GPIO21), U3.17 (DIAG)
unnamed: U2.32 (GPIO27_ADC1), U3.18 (VREF)
VCC: C4.1, J3.1, L1.2, U2.39 (VSYS), U4.4 (FB)

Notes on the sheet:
STEPPER TX/UX
ERC Flags
EXT MCU POWER
External power when USB is disconnected. 1.8-5.5 volts regulated by onboard Pico buck/boost.
LEFT Z-AXIS STEPPER CONTROL
EXPANSION PORT
Stepper motors can take anywhere between 9-24 volts. We'll just use a barrel jack and use a pre-built power supply. We need to put the switch on the front side so we need a P-Channel Mosfet. Since it's at 12 volts we need a N-Channel attached directly to GPIO 22 to control the P-channel. Include an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
For future interface so we don't need to recompile code to exercise and test motors.
Throw all the unused pins to a header so we can add in a few more components without having to respin the board.
UART Control Port
5 Volt Buck
EXT STEPPER POWER
RIGHT Z-AXIS STEPPER CONTROL
SOFT REBOOT SWITCH
Single wire RS483 style protocol is used to set advanced controls on TMC2209

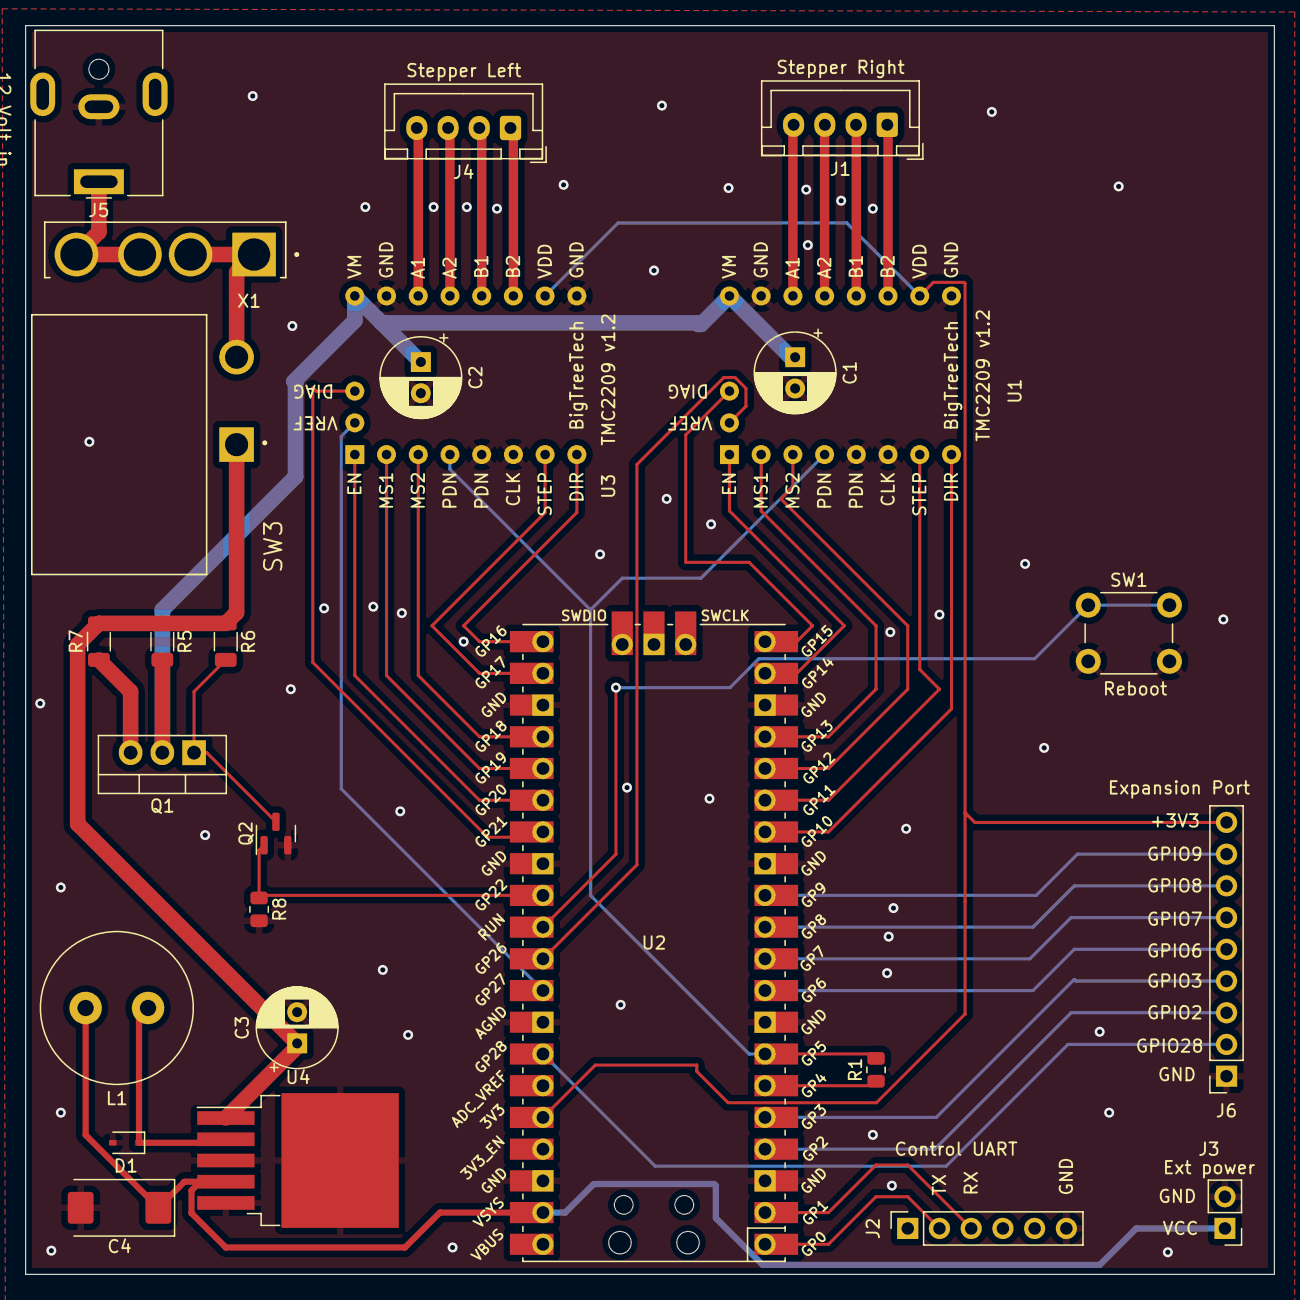
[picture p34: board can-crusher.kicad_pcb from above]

Board: 2 copper layers, 100.0 x 100.0 mm, 26 parts (0 on the bottom side), 45 nets.

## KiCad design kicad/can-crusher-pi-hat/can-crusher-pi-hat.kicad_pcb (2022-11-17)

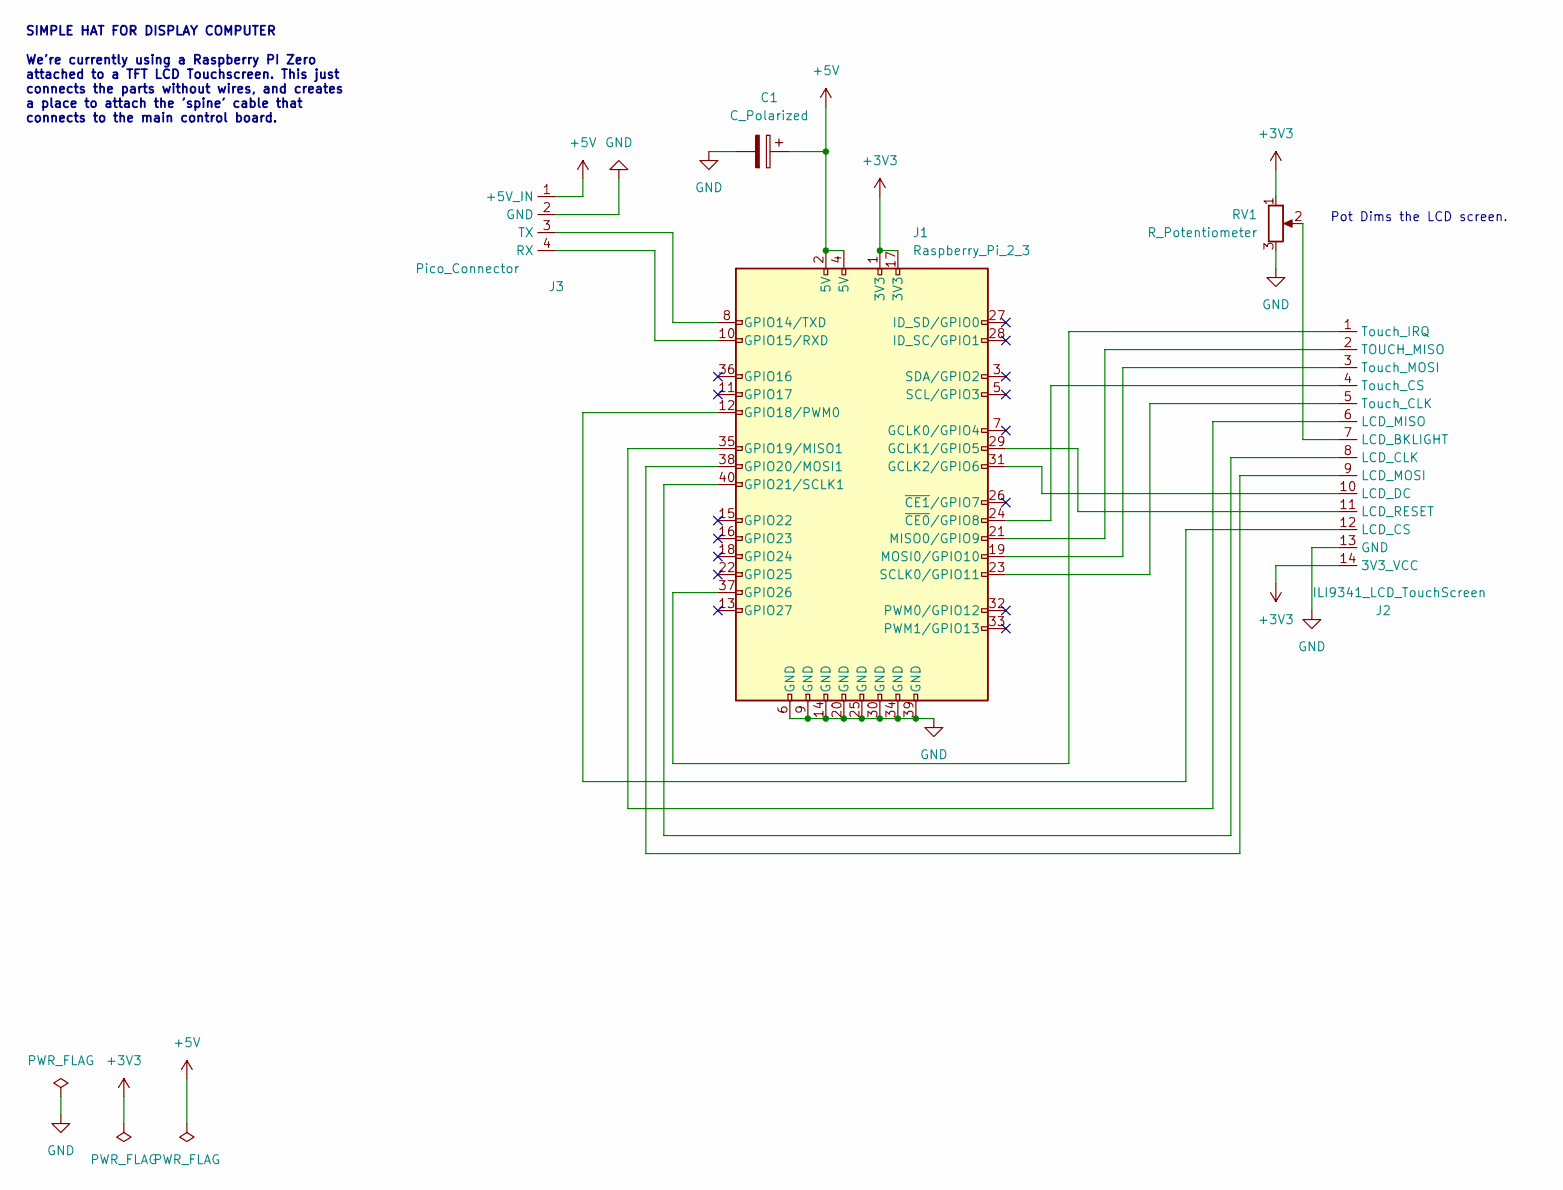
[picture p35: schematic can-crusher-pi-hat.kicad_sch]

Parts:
C1: C_Polarized; CP_Radial_D6.3mm_P2.50mm
J1: Raspberry_Pi_2_3; Raspberry_Pi_Zero_Socketed_THT_FaceDown_MountingHoles
J2: ILI9341_LCD_TouchScreen; PinSocket_1x14_P2.54mm_Vertical
J3: Pico_Connector; PinSocket_1x04_P2.54mm_Vertical
RV1: R_Potentiometer; Potentiometer_Runtron_RM-065_Vertical

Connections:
+3V3: J1.1 (3V3), J1.17 (3V3), J2.14 (3V3_VCC), RV1.1
+5V: C1.1, J1.2 (5V), J1.4 (5V), J3.1 (+5V_IN)
GND: C1.2, J1.6 (GND), J1.9 (GND), J1.14 (GND), J1.20 (GND), J1.25 (GND), J1.30 (GND), J1.34 (GND), J1.39 (GND), J2.13 (GND), J3.2 (GND), RV1.3
unnamed: J1.8 (GPIO14/TXD), J3.3 (TX)
unnamed: J1.10 (GPIO15/RXD), J3.4 (RX)
unnamed: J1.12 (GPIO18/PWM0), J2.12 (LCD_CS)
unnamed: J1.19 (MOSI0/GPIO10), J2.3 (Touch_MOSI)
unnamed: J1.21 (MISO0/GPIO9), J2.2 (TOUCH_MISO)
unnamed: J1.23 (SCLK0/GPIO11), J2.5 (Touch_CLK)
unnamed: J1.24 (~CE0/GPIO8), J2.4 (Touch_CS)
unnamed: J1.29 (GCLK1/GPIO5), J2.11 (LCD_RESET)
unnamed: J1.31 (GCLK2/GPIO6), J2.10 (LCD_DC)
unnamed: J1.35 (GPIO19/MISO1), J2.6 (LCD_MISO)
unnamed: J1.37 (GPIO26), J2.1 (Touch_IRQ)
unnamed: J1.38 (GPIO20/MOSI1), J2.9 (LCD_MOSI)
unnamed: J1.40 (GPIO21/SCLK1), J2.8 (LCD_CLK)
unnamed: J2.7 (LCD_BKLIGHT), RV1.2

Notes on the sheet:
SIMPLE HAT FOR DISPLAY COMPUTER We're currently using a Raspberry PI Zero attached to a TFT LCD Touchscreen. This just connects the parts without wires, and creates a place to attach the 'spine' cable that connects to the main control board.
Pot Dims the LCD screen.

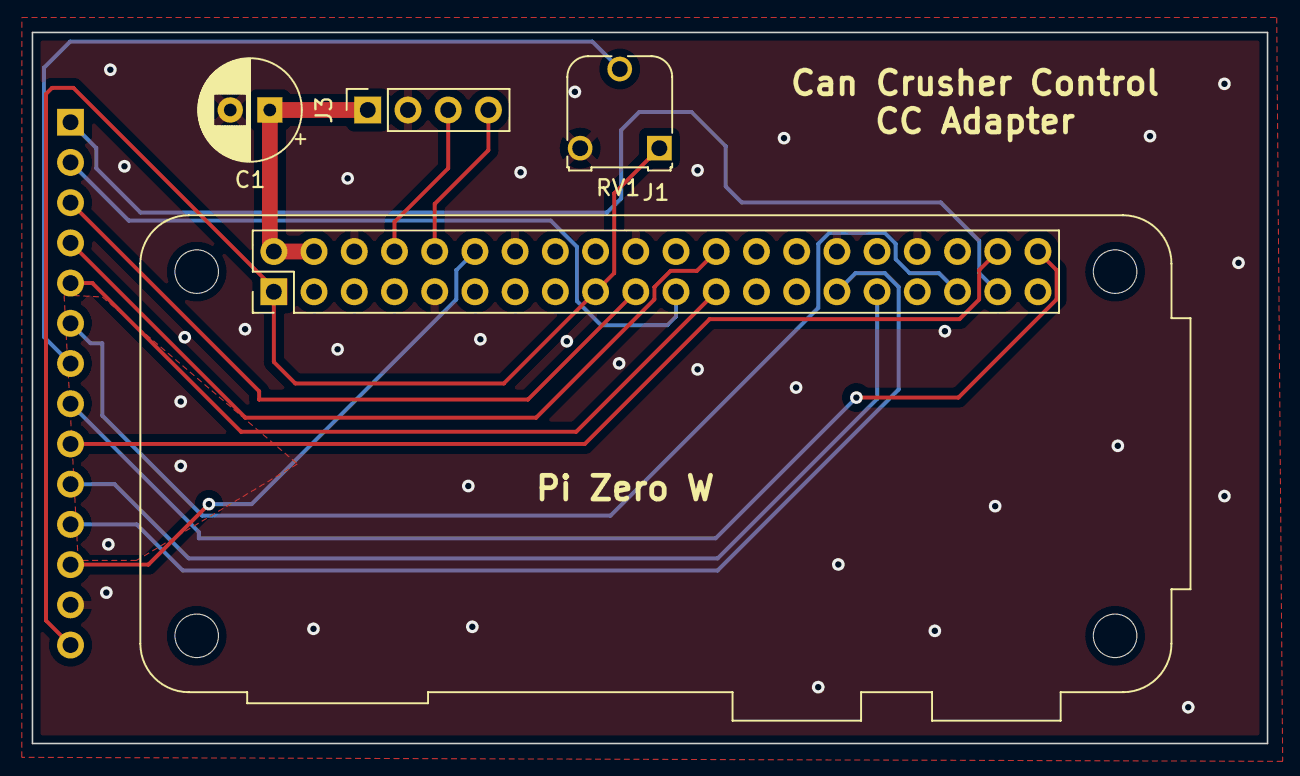
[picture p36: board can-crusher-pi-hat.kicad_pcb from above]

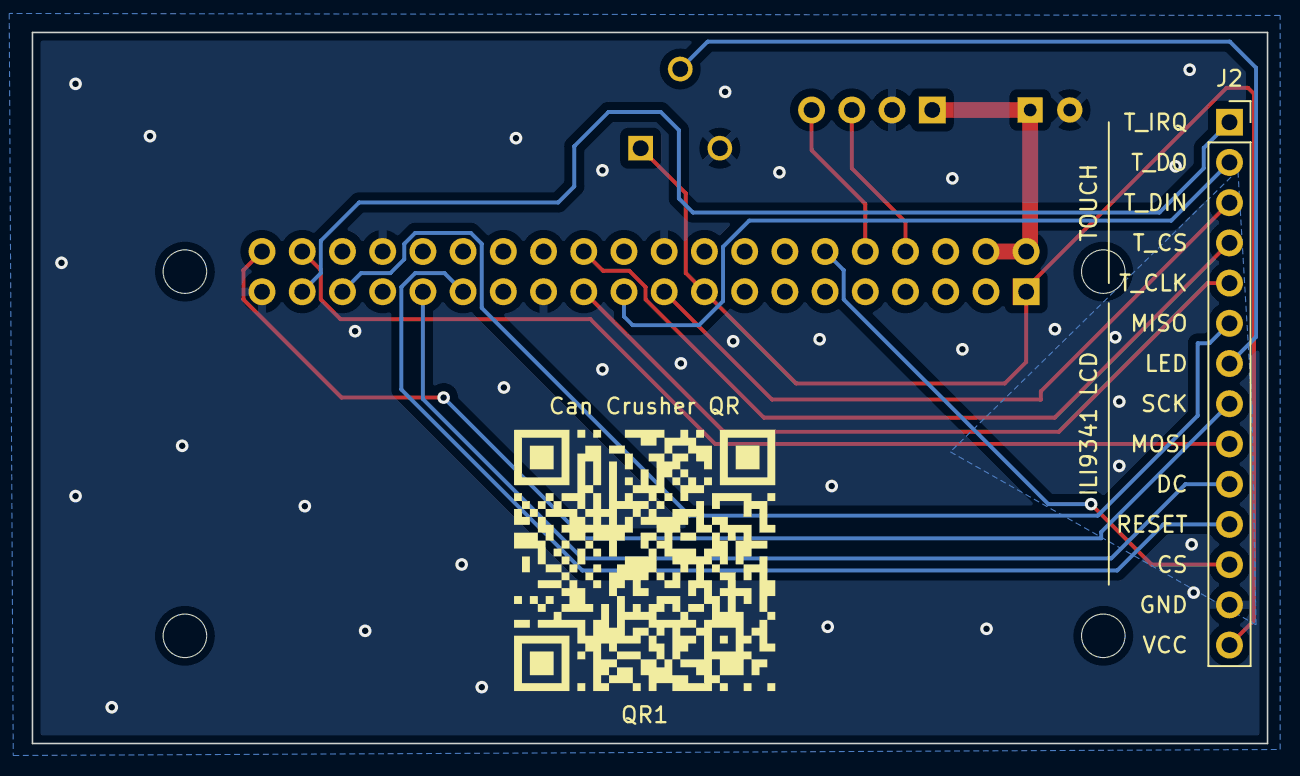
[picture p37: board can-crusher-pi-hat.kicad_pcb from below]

Board: 2 copper layers, 78.0 x 44.9 mm, 6 parts (3 on the bottom side), 17 nets.

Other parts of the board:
QR1: Can Crusher QR

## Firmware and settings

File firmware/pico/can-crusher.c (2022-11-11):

#include <stdio.h>
#include "pico/stdlib.h"
#include "hardware/gpio.h"
#include "pico/binary_info.h"
#include "led.h"
#include "button.h"
#include "power.h"
#include "motor.h"
#include "serial.h"
#include "property.h"
#include "power_management.h"

int main() {
  bi_decl(bi_program_description("Firmware for can crusher."));
  
  bi_decl(bi_1pin_with_name(LED_ONBOARD_PIN, "LED - Onboard"));
  bi_decl(bi_1pin_with_name(LED_RED_PIN, "LED - RGB Red"));
  bi_decl(bi_1pin_with_name(LED_GREEN_PIN, "LED - RGB Green"));
  bi_decl(bi_1pin_with_name(LED_BLUE_PIN, "LED - RGB Blue"));

  bi_decl(bi_1pin_with_name(USER_BUTTON_PIN, "User Interaction Button"));
  
  bi_decl(bi_1pin_with_name(LEFT_ENABLE_PIN, "Left Stepper Enable - active low."));
  bi_decl(bi_1pin_with_name(LEFT_STEP_PIN, "Left Stepper Step"));
  bi_decl(bi_1pin_with_name(LEFT_DIR_PIN, "Left Direction Step"));
  bi_decl(bi_1pin_with_name(LEFT_STALL_PIN, "Left Stall Step"));

  stdio_init_all();

  puts("STARTING INITIALIZATION");
  
  // Run first to immediately DISABLE the 12 volt power supply.
  // Don't leave it to chance.
  if(power_init()) {
    puts("power_init() failed! ABORTING!");
    return -1;
  }

  sleep_ms(500);
  
  if(property_init()) {
    puts("property_init() failed! ABORTING!");
    return -1;
  }

  if(led_init()) {
    puts("led_init() failed! ABORTING!");
    return -1;
  }
  
  if(button_init()) {
    puts("button_init() failed! ABORTING!");
    return -1;
  }

  if(serial_init()) {
    puts("serial_init() failed! ABORTING!");
    return -1;
  }
  
  puts("Enable 12V...");
  power_enable();

  if(motors_init()) {
    puts("motors_init() failed! ABORTING!");
    return -1;
  }
  
  if(power_management_init()) {
    puts("power_management_init() failed! ABORTING!");
    return -1;
  }
  
  // Boot sequence
  printf("Initialization complete. [BUILD: %s]\n", BUILD_ID);
  motors_wake();

  int home_speed = property_get_prop(PROP_HOME_SPEED);

  motors_move_mm(true, true, 5, home_speed);
  motors_sleep();
  sleep_ms(250);
  motors_wake();
  motors_move_mm(true, true, -5, home_speed);
  
  motors_sleep();
  
  serial_flush();
  while(1) {
    serial_process();
    power_management_tick();
    sleep_ms(100);
  };

  return 0;
}

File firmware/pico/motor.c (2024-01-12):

#include <stdio.h>
#include "pico/stdlib.h"
#include "hardware/gpio.h"
#include "pico/binary_info.h"
#include "hardware/uart.h"
#include "power.h"
#include "property.h"
#include "step.pio.h"
#include "motor.h"

static motor_t left_motor;
static motor_t right_motor;

static bool motor_awake = false;

static double motor_position = MOTOR_NOT_HOMED;

static PIO pio = pio0;
static uint offset_both, offset_one;

motor_t motor_init(motor_t *motor, 
                   uint enable, uint step, uint dir,
                   uint stall, uint device_id,
                   uint ms1_ad0, uint ms2_ad1) {
  motor->enable_pin = enable;
  motor->step_pin = step;
  motor->dir_pin = dir;
  motor->stall_pin = stall;
  motor->device_id = device_id;
  motor->ms1_ad0_pin = ms1_ad0;
  motor->ms2_ad1_pin = ms2_ad1;
  
  gpio_init(motor->enable_pin);
  gpio_set_dir(motor->enable_pin, GPIO_OUT);
  gpio_put(motor->enable_pin, 1);

  gpio_init(motor->step_pin);
  gpio_set_dir(motor->step_pin, GPIO_OUT);
  gpio_put(motor->step_pin, 0);

  gpio_init(motor->dir_pin);
  gpio_set_dir(motor->dir_pin, GPIO_OUT);
  gpio_put(motor->dir_pin, 0);

  gpio_init(motor->stall_pin);
  gpio_set_dir(motor->stall_pin, GPIO_IN);
  gpio_set_pulls(motor->stall_pin, false, true);
  
  gpio_init(motor->ms1_ad0_pin);
  gpio_set_dir(motor->ms1_ad0_pin, GPIO_OUT);
  gpio_put(motor->ms1_ad0_pin, 0);

  gpio_init(motor->ms2_ad1_pin);
  gpio_set_dir(motor->ms2_ad1_pin, GPIO_OUT);
  gpio_put(motor->ms2_ad1_pin, 0);

}

void motor_enable(motor_t *motor) {
  gpio_put(motor->enable_pin, 0);
}

void motor_disable(motor_t *motor) {
  gpio_put(motor->enable_pin, 1);
}

void motor_step(motor_t *motor, int step_duration_us) {
  gpio_put(motor->step_pin, 1);
  sleep_us(step_duration_us/2);
  gpio_put(motor->step_pin, 0);
  sleep_us(step_duration_us/2);
}

void motor_set_dir(motor_t *motor, uint dir) {
  gpio_put(motor->dir_pin, dir);
}

int motor_is_stalled(motor_t *motor) {
  return gpio_get(motor->stall_pin) != 0;
}

void motor_control_init() {
  uart_init(MC_UART_ID, MC_BAUD_RATE);
  gpio_set_function(4, GPIO_FUNC_UART);
  gpio_set_function(5, GPIO_FUNC_UART);
}

void motor_control_crc(char* buffer, int size) {
  uint8_t crc = 0;

  // Last byte holds the crc, ignore from calc
  for (int i=0;i<size-1;i++) {
    uint8_t byte = buffer[i];
    // process byte bit-by-bit
    for (int j=0;j<8;j++) {
      if ( (crc >> 7) ^ (byte & 0x1) ) {
        crc = (crc << 1) ^ 0x07;
      } else {
        crc = crc << 1;
      }
      
      byte = byte >> 1;
    }
  }

  buffer[size-1] = crc;
}

// Sending and receiving data has BLOCKING calls. All configuration
// Should be done before we start moving motors.
int motor_control_tx_data(motor_t *motor, char* buffer, int size) {
  sleep_ms(100); //Seems to get mad if we talk to two different chips to quickly, wait a bit.
  
  motor_control_crc(buffer, size);

  while(uart_is_readable(MC_UART_ID)){ uart_getc(MC_UART_ID); }

  uart_write_blocking(MC_UART_ID, buffer, size);
  uart_tx_wait_blocking(MC_UART_ID);
  
  // read back identical data, since we're sharing a uart line.
  char dummy_char;
  for (int i=0;i<size;i++) {
    if (uart_is_readable(MC_UART_ID)) {
      dummy_char = uart_getc(MC_UART_ID);
      if (dummy_char != buffer[i]) {
        printf("CHAR %d DIDN'T MATCH. Expected 0x%x, Got 0x%x\n", buffer[i], dummy_char);
        return -1;
      }
    } else {
      puts("ERROR READING UART, NO DATA\n");
      return -1;
    }
  }
  return 0;
}

int motor_control_register_read(motor_t *motor, uint8_t reg, uint32_t *result) {
  static char read_buffer[4] = {0x05, 0x00, 0x00, 0x00};
  static char result_buffer[8];

  read_buffer[1] = motor->device_id;
  read_buffer[2] = reg;

  if(motor_control_tx_data(motor, read_buffer, 4)) {
    puts("ERROR SENDING!");
    return -1;
  }

  if(!uart_is_readable_within_us(MC_UART_ID, 10000)) {
    puts("NO RESPONSE!");
    return -1;
  }
  
  uart_read_blocking(MC_UART_ID, result_buffer, 8);
 
  char result_crc = result_buffer[7];
  motor_control_crc(result_buffer, 8);

  if (result_buffer[7] != result_crc) {
    puts("BAD RECALCULATED CRC");
    return -1;
  }
  
  if ((result_buffer[0] & 0x0F) != 5) {
    puts("BAD SYNC FIELD");
    return -1;
  }

  if (result_buffer[1] != 0xFF) {
    puts("BAD ID FIELD");
    return -1;
  }

  *result = (result_buffer[3] << 24) | (result_buffer[4] << 16) |
    (result_buffer[5] << 8) | result_buffer[6];

  return 0;
}

bool motor_control_register_write(motor_t *motor, uint8_t reg, uint32_t value) {
  static char write_buffer[8] = {0x05, 0x00, 0x00, 0x00, 0x00, 0x00, 0x00, 0x00};

  write_buffer[1] = motor->device_id;
  write_buffer[2] = reg + 128;
  write_buffer[3] = (value >> 24) & 0xFF;
  write_buffer[4] = (value >> 16) & 0xFF;
  write_buffer[5] = (value >> 8) & 0xFF;
  write_buffer[6] = value & 0xFF;

  
  return motor_control_tx_data(motor, write_buffer, 8);
}


void motor_control_enable() {
  // Can't step while we change the device IDs.
  motor_disable(&left_motor);
  motor_disable(&right_motor);

  printf("LEFT: ID %d BIT1 %d BIT2 %d\n", left_motor.device_id, left_motor.device_id & 1,
         left_motor.device_id & 2);
  gpio_put(left_motor.ms1_ad0_pin, left_motor.device_id & 0x1);
  gpio_put(left_motor.ms2_ad1_pin, left_motor.device_id & 0x2);

  printf("RIGHT ID %d BIT1 %d BIT2 %d\n", right_motor.device_id, right_motor.device_id & 1,
         right_motor.device_id & 2);
  gpio_put(right_motor.ms1_ad0_pin, right_motor.device_id & 0x1);
  gpio_put(right_motor.ms2_ad1_pin, (right_motor.device_id & 0x2) == 2);

}

void motor_control_disable() {
  // set back to stepping mode
  gpio_put(left_motor.ms1_ad0_pin, 0);
  gpio_put(left_motor.ms2_ad1_pin, 0);

  gpio_put(right_motor.ms1_ad0_pin, 0);
  gpio_put(right_motor.ms2_ad1_pin, 0);

  // Still don't explicitly enable.
}  

bool motor_control_stallguard(motor_t *motor) {
  uint32_t motor_write_counter_start;
  uint32_t motor_write_counter_finish;

  if (motor_control_register_read(motor, 0x2, &motor_write_counter_start)) {
    puts("Couldn't read counter START");
    return false;
  }

  uint32_t tcoolthrs = property_get_prop(PROP_TCOOL_THRESHOLD);
  uint32_t sgthrs = property_get_prop(PROP_STALLGUARD_THRESHOLD);

  motor_control_register_write(motor, 0x14, tcoolthrs);
  motor_control_register_write(motor, 0x40, sgthrs);

  if (motor_control_register_read(motor, 0x2, &motor_write_counter_finish)) {
    puts("Couldn't read counter FINISH");
    return false;
  }

  // puts("GOT FINISH");
  if (motor_write_counter_finish - motor_write_counter_start != 2) {
    puts("Counted WRITES doesn't add up");
    return false;
  } else {
    return true;
  }
}

void query_register(motor_t *left_motor, uint8_t address) {
  uint32_t test_result;
  if (!motor_control_register_read(left_motor, address, &test_result)) {
  
    printf("Register %x  data %08x\n", address, test_result);
  } else {
    printf("Register %x FAIL\n", address, test_result);
  }
}
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

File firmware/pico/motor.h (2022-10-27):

#ifndef __MOTOR_H__
#define __MOTOR_H__


// Specifically, the UART that we use to set STALLGUARD
#define MC_UART_ID uart1 
#define MC_BAUD_RATE 115200

#define LEFT_DIR_PIN 16
#define LEFT_STEP_PIN 17
#define LEFT_MS2_AD1_PIN 18
#define LEFT_MS1_AD0_PIN 19
#define LEFT_ENABLE_PIN 20
#define LEFT_STALL_PIN 21

#define LEFT_DEVICE_ID 1

#define RIGHT_DIR_PIN 10
#define RIGHT_STEP_PIN 11
#define RIGHT_MS2_AD1_PIN 12
#define RIGHT_MS1_AD0_PIN 13
#define RIGHT_ENABLE_PIN 14
#define RIGHT_STALL_PIN 15

#define RIGHT_DEVICE_ID 2

#define STEP_PIO_SM_BOTH 0
#define STEP_PIO_SM_ONE 1

#define STEP_STRATEGY_PIO true // False to use naive strategy which doesn't have precise timing

// Use an excessively large negative number here.
// We might have some drift on undetected stalls,
// but not 1000 times the height of the whole device
#define MOTOR_NOT_HOMED -400000

typedef struct {
  uint enable_pin;
  uint step_pin;
  uint dir_pin;
  uint stall_pin;
  uint device_id;  // Slave, but done with slave terminology
  uint ms1_ad0_pin;
  uint ms2_ad1_pin;
} motor_t;

int motors_move_mm(bool left, bool right, int mm, int mm_per_second);
int motors_init();
int motors_home();

int motors_wake();
int motors_sleep();

bool motors_is_awake();

double motors_get_position();

void motors_zero_position();
void motors_invalidate_position();

#endif

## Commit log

2022-09-27 Initial checkin of FreeCAD files
    [can-crusher.FCStd, frame-plates.stl]
2022-09-27 Add test for parts that must go in to extruded rails
    [can-crusher.FCStd, test-rail-guide.stl]
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2022-09-28 Add 3d printed base to go under CNCed base, so we can countersink installation screws and add feet to the base.
    [base-with-feet.stl, can-crusher.FCStd]
2022-09-29 Add bill of materials
    [Bill of Materials.ods]
2022-09-29 Finish up servo holder add mounting holes for M3 screws
    [can-crusher.FCStd, servo-holder.stl]
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2022-09-29 Fix servo holder hole which got filled back in.
    [can-crusher.FCStd, servo-holder.stl]
2022-09-30 More refinements to design
    [can-crusher.FCStd, crusher-plate.stl, frame-plates.stl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]
2022-10-02 Match acrylic parts to thickness of my stock. Save good copies as step for ease in CNC path layout
    [can-crusher.FCStd, frame-ends.step]
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2022-10-07 Adjust crusher plate to work with motors.
    [can-crusher.FCStd, crusher-plate.stl]
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2022-10-07 Stall Detection, left motor only.
    [can-crusher.c]
2022-10-07 All code to detect stalls on both motors
    [can-crusher.c]
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2022-10-07 Basic homing code. Need to figure out why stall status isn't clearing out on motor reset
    [can-crusher.c]
2022-10-07 Add step file of cnc test part
    [lead_holder_test.step]
2022-10-07 Step file for crusher element
    [crusher-element.step]
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2022-10-09 Test part to add weight to crusher element
    [can-crusher.FCStd]
2022-10-09 Change cad dir to differentiate from KiCad PCB directory
    [can-crusher.FCStd]
2022-10-10 Initial kicad project with external Pi Pico reference
    [can-crusher.kicad_pcb, can-crusher.kicad_sch]
2022-10-10 Added pico to schematic, really just testing that git works well between OSes
    [can-crusher.kicad_sch]
2022-10-10 Schematic Work in progress
    [can-crusher.kicad_sch]
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2022-10-10 Initial first pass of PCB design
    [can-crusher.kicad_sch]
2022-10-11 Added title comments, etc, to title block
    [can-crusher.kicad_sch]
2022-10-11 Fix VREF setting on Pico layout
2022-10-11 Fixes for ERC checks
    [can-crusher.kicad_sch]
2022-10-11 Add can holder at base so can doesn't pop out
    [can-crusher.FCStd, can-holder.stl, weight-tray.stl]
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2022-10-11 More tweaks to 12 enable circuitry;First round of assigning all footprints
    [can-crusher.kicad_sch]
2022-10-11 Rough out initial rats nest; Change pin assignments to make layout easier.
    [can-crusher.kicad_pcb, can-crusher.kicad_sch]
2022-10-11 Give better name to project lib storage dir
    [can-crusher.kicad_pcb, can-crusher.kicad_sch]
2022-10-12 Make board more compact; make power traces appropriate sized.
    [can-crusher.kicad_pcb, can-crusher.kicad_sch]
2022-10-12 Final REV 1 control board submitted for PCB manufacturing
    [can-crusher-B_Cu.gbr, can-crusher-B_Mask.gbr, can-crusher-B_Paste.gbr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]
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2022-10-13 PCB Vendor requested 0.5mm spacing between RGB LED holes by making holes 0.75mm instead of 0.9mm
    [can-crusher.kicad_pcb]
2022-10-14 Modify crusher design for laser cut aluminum
    [can-crusher.FCStd, crusher-element-cnc.step, crusher-element-laser.step]
2022-10-15 Servo holders needed clearance for JST connector
    [can-crusher.FCStd, servo-holder.stl]
2022-10-17 Fix pin assignments based on new schmatic.
    [can-crusher.c]
2022-10-17 Test optional power and fix problem with new pin assignment, test motors
    [can-crusher.c]
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2022-10-18 Fix initialization sequence. Fix bug in speeds running both motors at once
    [can-crusher.c, motor.c]
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2022-10-18 Have all _init methods return success/failure codes, and check these, even if they're not needed yet
    [can-crusher.c, led.c, led.h]
2022-10-18 Export stl with tapered base feet
    [base-with-feet.stl, can-crusher.FCStd]
2022-10-18 Debounce stall detection until we figure out how to correctly clear stalls.
    Handle motor subsystem with motors_wake and motors_sleep.
    Add WAKE and SLEEP commands to the Serial CLI.
    [can-crusher.c, motor.c, motor.h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]
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2022-10-19 Treat motor stalling as an error condition in the CLI
    [serial.c]
2022-10-19 Move serial error codes to header file
    [serial.c]
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2022-10-19 make more specific stall warnings telling the trigger.
    [serial.c]
2022-10-19 Simpler logic for problem where motors stall immediately
    [motor.c]
2022-10-19 Initial case for dev PCB
    [can-crusher.FCStd, pcb-holder-lid.stl, pcb-holder.stl]
2022-10-19 Old rod support was too tight and sqeaky. Give some more tolerance in the hole. Make it longer to compensate. Allow user to see the screw through the top opening.
    [can-crusher.FCStd, rod-holder.stl]
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2022-10-20 Add facility to store values as properties, use them for the stallguard settings in the motor unit, allow users to get and set properties in serial console.
    [can-crusher.c, motor.c, property.c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]
2022-10-20 Improve homing. Allow homing to report a failure
    [motor.c, motor.h, serial.c]
2022-10-21 Move step settings and stallguard enable settings to properties
    [motor.c, motor.h, property.c]
2022-10-24 Make pcb case thinner, and assume we're surface mounting the Pico
    [can-crusher.FCStd, pcb-holder-high-pico.stl, pcb-holder-lid.stl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]
2022-10-24 Add pull down to power circuitry
    [can-crusher.kicad_pcb, can-crusher.kicad_sch]
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2022-10-25 Make home parameters tunable; add cli method RESET_PROPS to restore factory defaults
    [motor.c, property.c, serial.c]
2022-10-25 Improve script that profiles stallguard numbers
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2022-10-27 Proper tuning of TCOOLTRSH fixes the issue where motors stall on initial movement
    [motor.c, property.c]
2022-10-27 Track distance, detect proper stalls, in pop motor movement
    [motor.c]
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2022-10-31 Tweaks to make sure Rod holder and servo holder line up with crusher plate
    [can-crusher.FCStd, rod-holder.stl, servo-holder.stl]
2022-11-02 Vertical bearing holder for smooth rods
    [can-crusher.FCStd, vertical-bearing-holder.stl]
2022-11-02 Modified crusher element for smooth rods
    [can-crusher.FCStd, crusher-element-with-bearing-holders.step, crusher-element-with-bearing-holders.stl]
2022-11-02 Modify can holder to also hold smooth rods
    [can-crusher.FCStd, can-holder-with-smooth-rod-holder.stl]
2022-11-06 Screw holes on vertical bearing holder were a little too close to the edge.
    [can-crusher.FCStd, vertical-bearing-holder.stl]
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2022-11-07 Clean up full cad view to reflect current design.
    [can-crusher.FCStd]
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2022-11-08 Stabilize stallguard test code
    [motor.c]
2022-11-08 Fixes for binding stepper motion:
    1. Put slots instead of holes on the stepper holder so we can manually true it.
    2. Rod holders SHOULD allow a lot of play, and just stop rods when something has gone horribly wrong.
    [can-crusher.FCStd, rod-holder.stl, servo-holder.stl]
2022-11-08 Give stepper holder stl correct name
    [stepper-holder.stl]
2022-11-08 Make sure int values are ints, atoi() doesn't have error conditions
    [serial.c]
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2022-11-11 Add power management so we don't burn out steppers
    [can-crusher.c, power_management.c, serial.c]
2022-11-11 Remove buffer space on smooth rod holders. The rods would move around.
    [can-crusher.FCStd, smooth-rod-holder-top.stl]
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2022-11-17 Rename some board files now that we have two boards.
    [can-crusher-B_Cu.gbr, can-crusher-B_Mask.gbr, can-crusher-B_Paste.gbr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]
2022-11-17 Display PCB hat to connect Pi Zero and TFT LCD
    [can-crusher-pi-hat-B_Cu.gbr, can-crusher-pi-hat-B_Mask.gbr, can-crusher-pi-hat-B_Paste.gbr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]
2022-11-17 Final dial in of touch screen holder settings
    [can-crusher.FCStd, touch-screen-front.stl]
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2022-11-19 Fix import after moving code to package
    [touch_screen.py]
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2022-11-21 Move PiHat folder to a sibling folder of original KiCad project
    [can-crusher-pi-hat.kicad_pcb, can-crusher-pi-hat.kicad_sch]
2022-11-21 Fixed stupid, stupid wiring error with serial control. Reverted screen to normal position and have pi use /dev/serial0
    [spi_display.py]
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2022-11-21 Production PCB lid, no big gap to access dev buttons
    [can-crusher.FCStd, pcb-holder-lid.stl]
2022-11-22 Fixes for slide refactor
    [display_helper.py]
2022-11-22 Test to make sure we talk to Pico. Throw error if we're not connected
    [display_helper.py, serial_cli.py]
2022-11-22 Catch another error case
    [can_crusher.py]
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2022-11-24 Remove RGB led and button; add free pins to header; add ADC pins to the TMC2209 VREF pins for future use
    [can-crusher.kicad_pcb, can-crusher.kicad_sch]
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2022-11-24 Renamed alternate parts to make it clear you should print one or the other
    [ALT-pcb-holder-lid-with-dev-button-access.stl, ALT-pcb-holder-pico-on-header-socket.stl]
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2022-11-25 Move gerbers to top level directory so they're easy to find, and in the same basic area users will find STL and STEP files
    [can-crusher-B_Cu.gbr, can-crusher-B_Mask.gbr, can-crusher-B_Paste.gbr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]
2024-01-12 Allow config to store individual unit's stallguard threshold
    [can_crusher.py]
2024-01-12 Always set ui.stallguard_threshold
2024-01-12 New homing strategy. Don't try to be too smart. Just go til we stall 4 times, assuming the rails get closer each time.
    [motor.c]
